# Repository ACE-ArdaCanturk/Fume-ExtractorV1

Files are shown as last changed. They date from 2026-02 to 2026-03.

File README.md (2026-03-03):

# Fume-ExtractorV1

This project wasn't originally meant to be shared and was more so something I built with parts I had on hand. This is why it includes weird parts like a neon bulb or a non standard inline fan, but I figured I might as well share it if anyone for some reason happened to have these parts on hand and wanted to build it, or to at least draw some inspiration for their own projects. It is a fume extractor for soldering consisting of one inline fan module with a 100mm radial fan and a bellmouth intake.

[Assembly Guide](AssemblyInstructions.md)

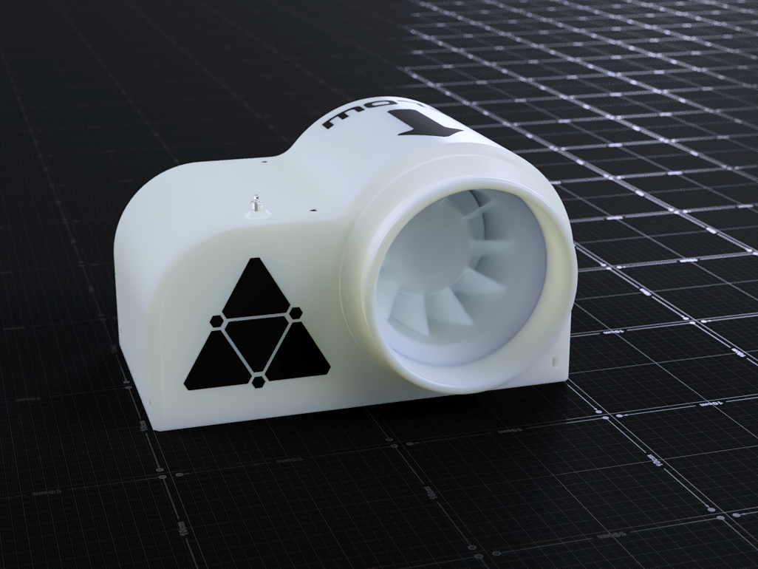
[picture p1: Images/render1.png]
Render1


# Media

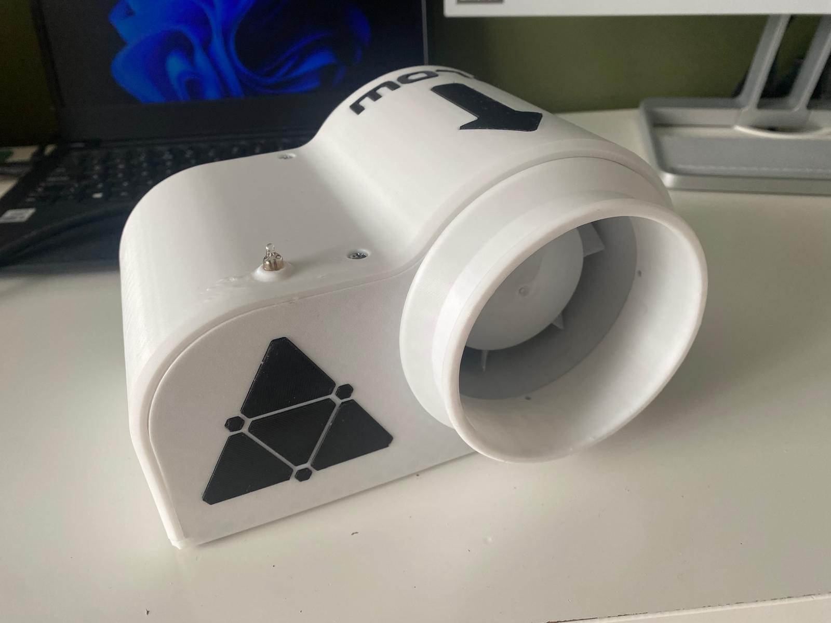
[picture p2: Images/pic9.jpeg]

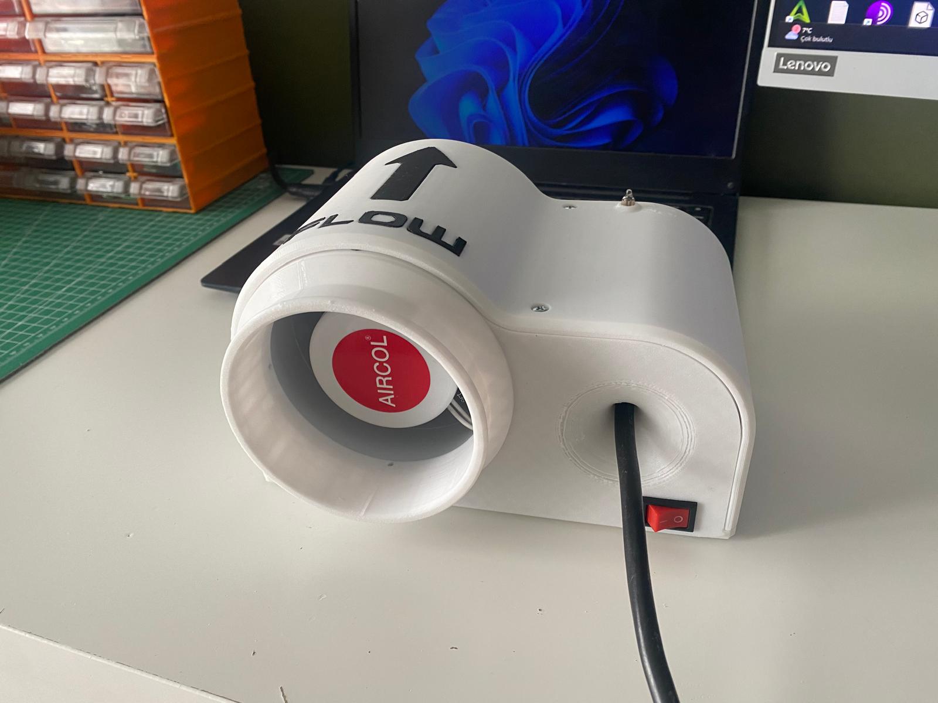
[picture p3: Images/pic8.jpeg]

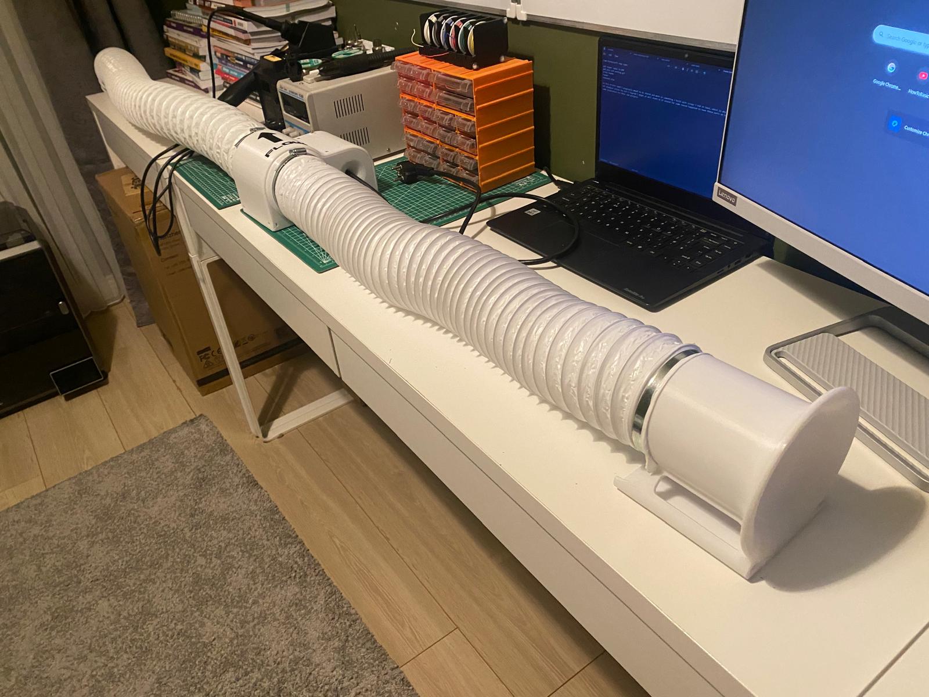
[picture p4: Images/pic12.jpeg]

gif2

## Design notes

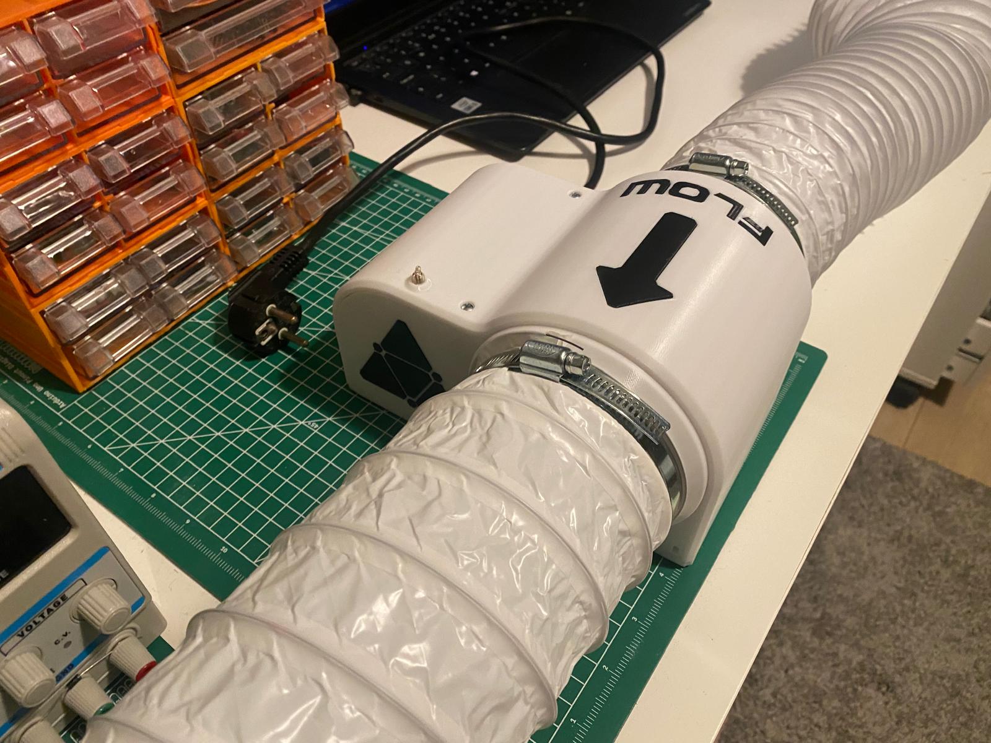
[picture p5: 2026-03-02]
Images/pic11.jpeg

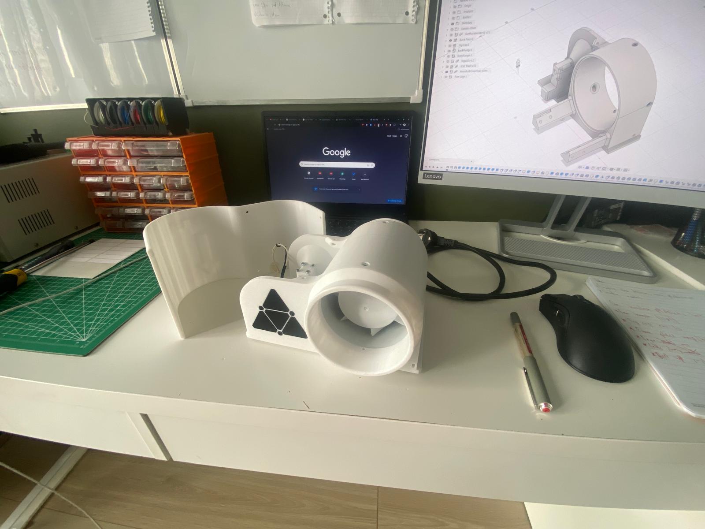
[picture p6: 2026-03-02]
Images/pic2.jpeg

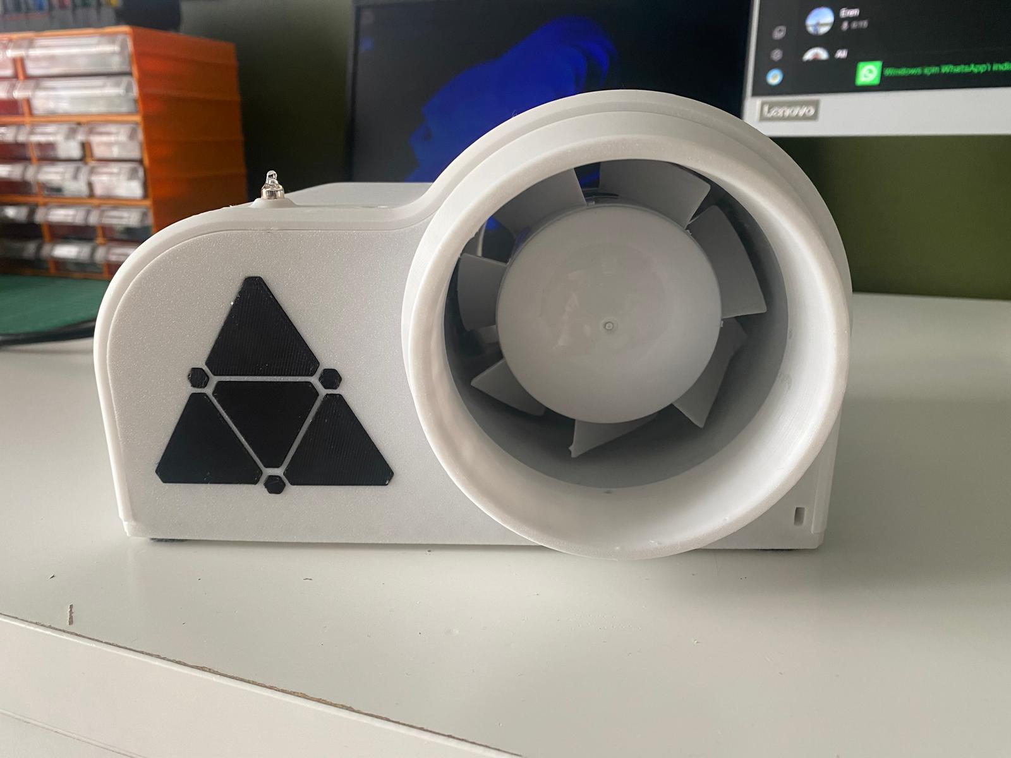
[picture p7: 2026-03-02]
Images/pic7.jpeg

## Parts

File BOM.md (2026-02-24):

## Bill of Materials (BOM): Fume-ExtractorV1

| Part Name | Description | Quantity | Link/Source |
| :--- | :--- | :--- | :--- |
| **Aircol 100KT** | 100mm AC Inline Fan | 1 | [Aksa Motor Fan](https://www.aksamotorfan.com/tr-TR/catalogue/kt-serisi/aircol-100-kt/1060/69) |
| **HVAC Tubing** | ID 100mm, Length 2000mm (200cm) | 2 | Local Hardware |
| **Hose Clamp** | 90-110mm Adjustable | 3 | Local Hardware |
| **Wago Connector** | 2-Pin Splicing Connector | 1 | Local Electronics |
| **AC Screw Terminal** | Wire-to-Wire Terminal Block | 1 | Local Electronics |
| **KCD1-101 Switch** | Rocker On/Off Switch | 1 | Local Electronics |
| **Neon Indicator** | 5mm Neon Lamp | 1 | Local Electronics |
| **AC Cable** | Standard Power Cord | 1 | Local Electronics |
| **M3x25mm Screw** | Roundhead Machine Screw | 2 | Local Hardware |
| **M3x20mm Screw** | Roundhead Machine Screw | 4 | Local Hardware |
| **M3x10mm Screw** | Roundhead Machine Screw | 11 | Local Hardware |
| **M3x5mm Screw** | Roundhead Machine Screw | 8 | Local Hardware |
| **M3 Nut** | Standard Hex Nut | 17 | Local Hardware |

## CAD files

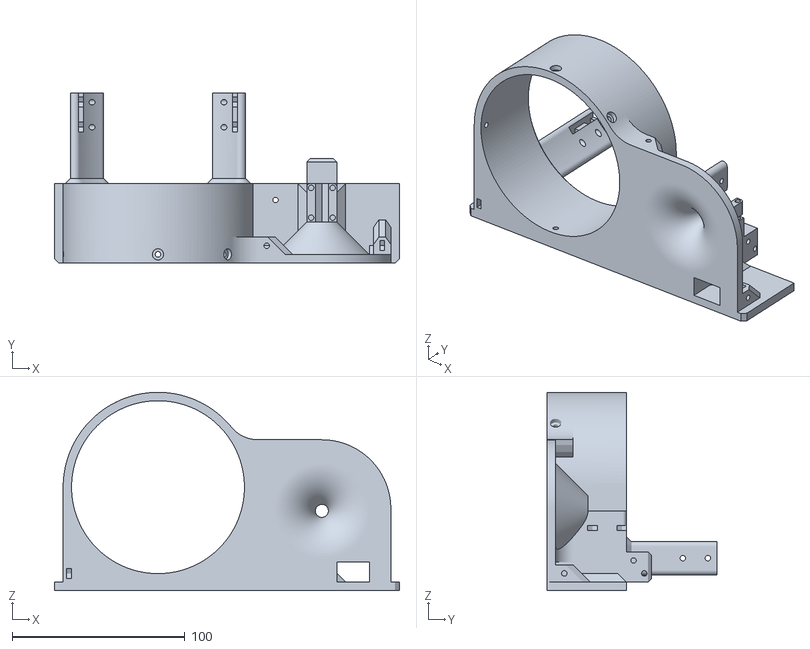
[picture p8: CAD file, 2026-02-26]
STLs/mainStructureBackPart.stl
200.0 x 98.5 x 115.0

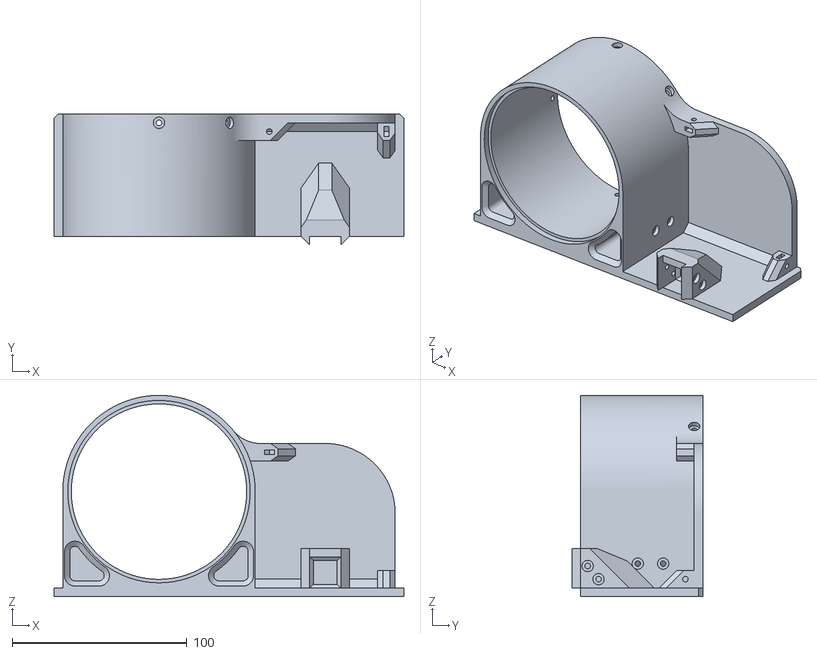
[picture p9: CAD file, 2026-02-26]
STLs/mainStructureFrontPart.stl
200.0 x 74.8 x 115.0

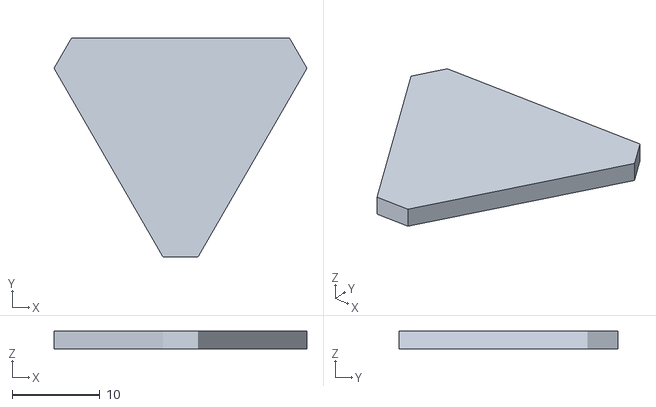
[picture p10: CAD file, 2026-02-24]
STLs/Lettering/logoMiddleTriangle.stl
28.9 x 25.0 x 2.00

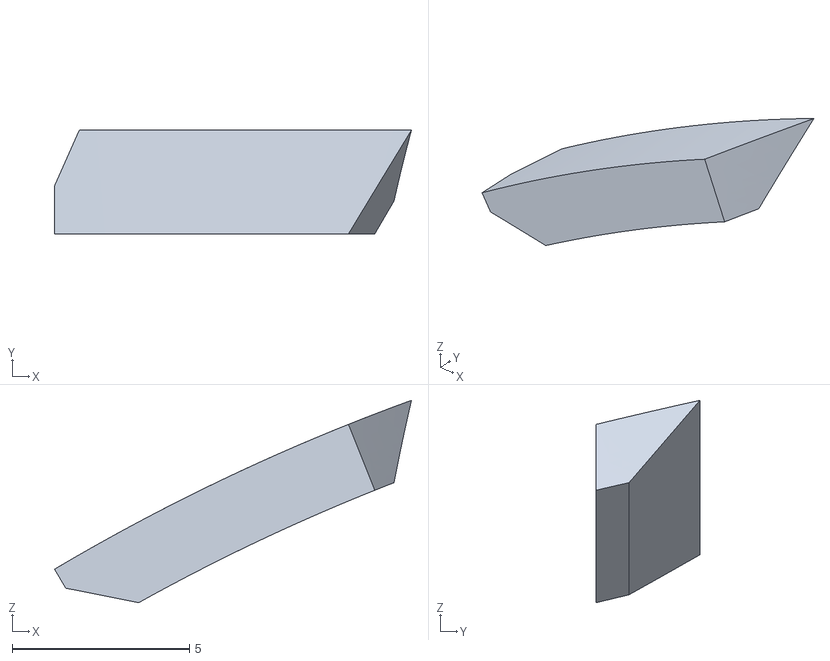
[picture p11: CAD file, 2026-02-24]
STLs/Lettering/letterFpart2.stl
10.1 x 2.93 x 5.71

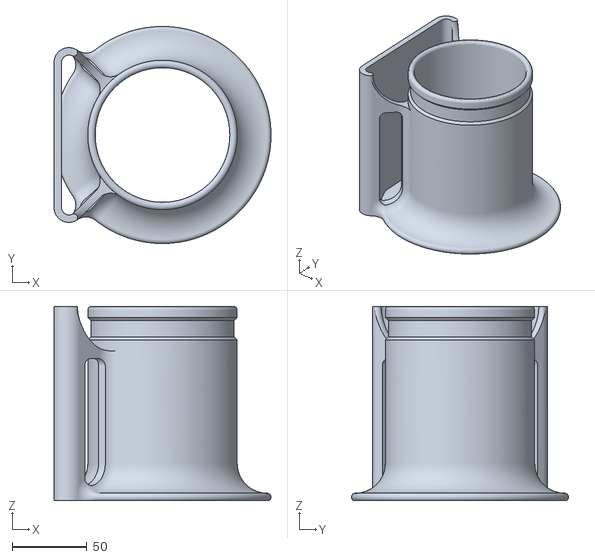
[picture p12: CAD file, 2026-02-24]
STLs/bellmouthIntake.stl
145.2 x 145.2 x 130.0

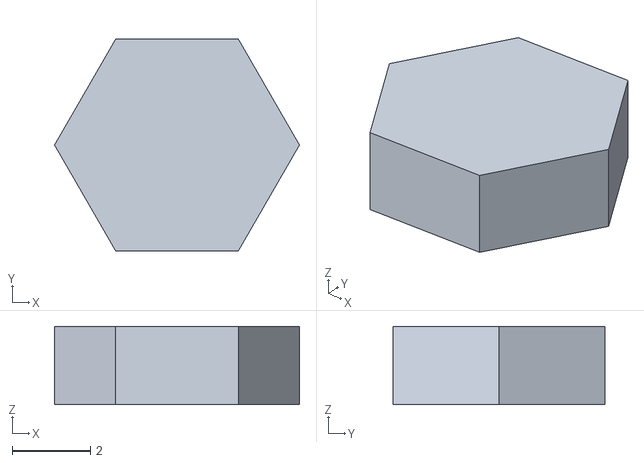
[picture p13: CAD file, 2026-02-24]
STLs/Lettering/logoHexagon3x.stl
6.27 x 5.43 x 2.00

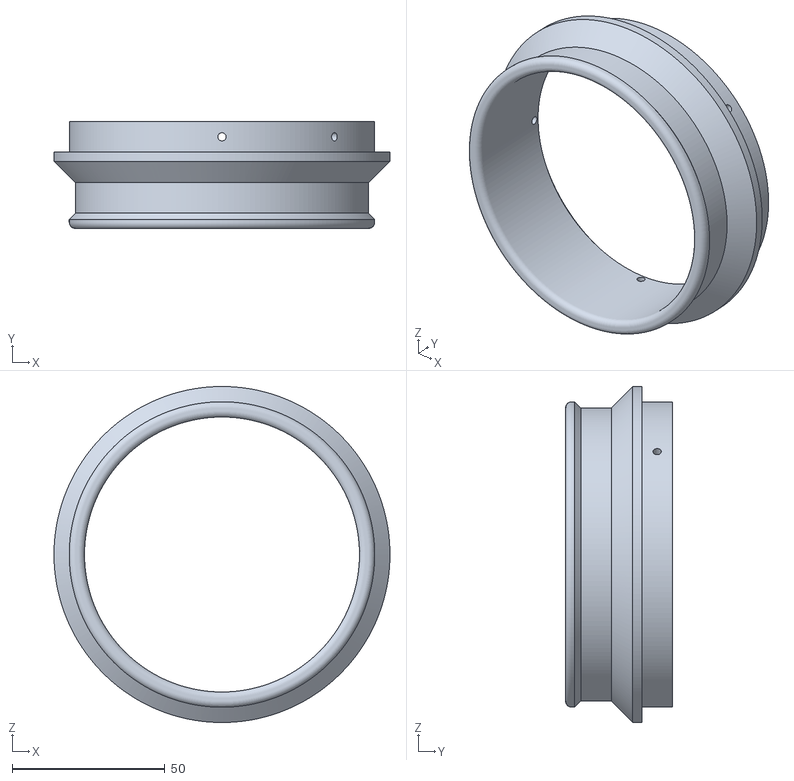
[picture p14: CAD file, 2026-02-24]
STLs/backFlange.stl
110.0 x 35.0 x 110.0

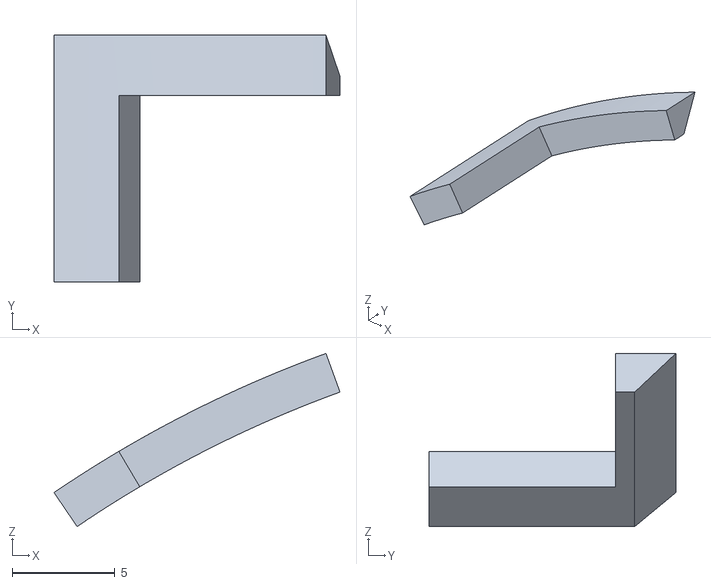
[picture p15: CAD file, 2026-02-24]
STLs/Lettering/letterFpart1.stl
13.9 x 12.0 x 8.43

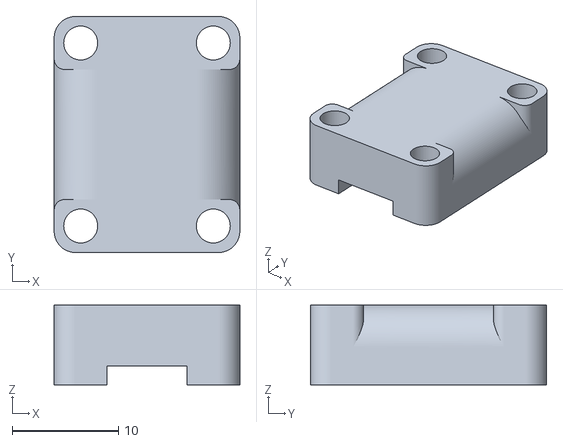
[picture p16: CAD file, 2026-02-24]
STLs/c_clamp.stl
17.5 x 22.2 x 7.50

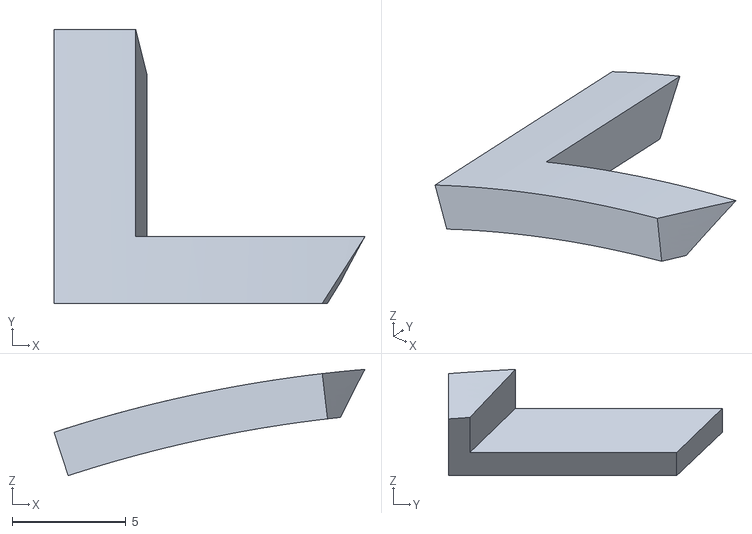
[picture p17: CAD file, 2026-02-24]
STLs/Lettering/letterL.stl
13.6 x 12.0 x 4.67

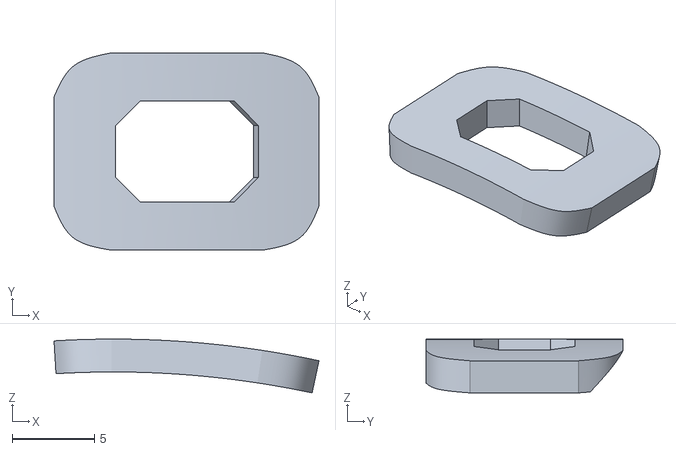
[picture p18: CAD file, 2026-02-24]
STLs/Lettering/letterO.stl
16.1 x 12.0 x 3.27

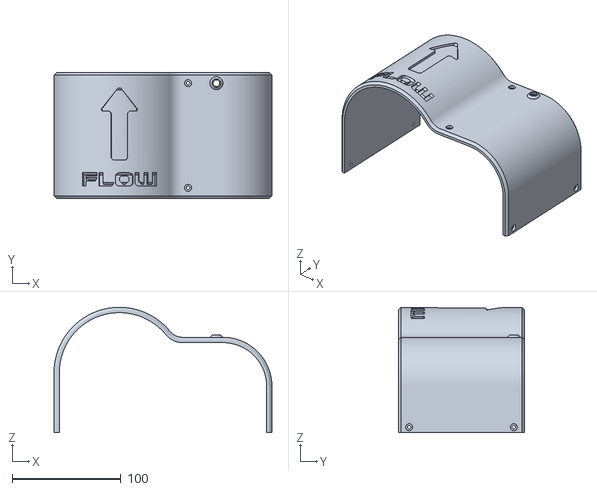
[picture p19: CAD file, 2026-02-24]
STLs/topCover.stl
200.0 x 116.0 x 115.0

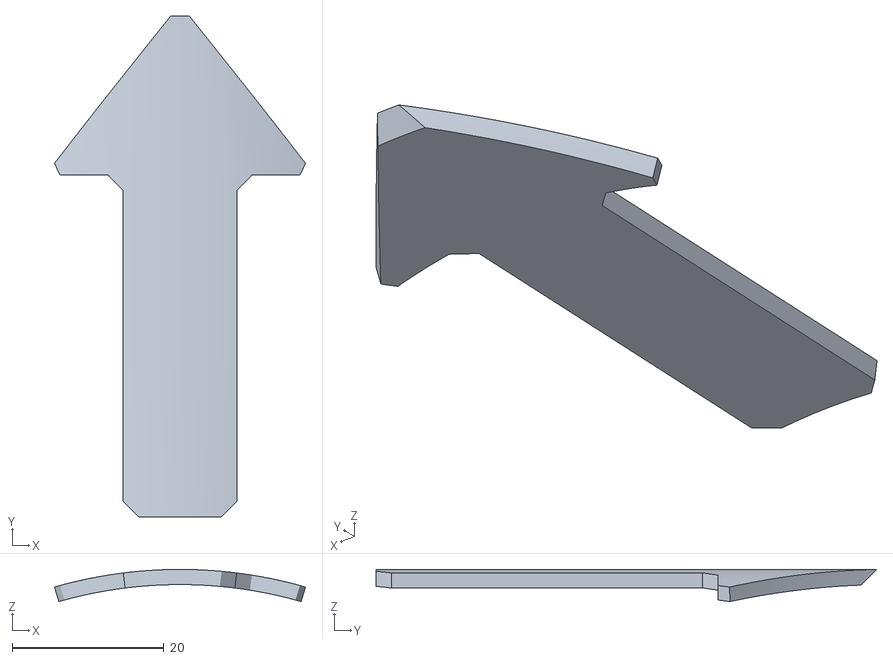
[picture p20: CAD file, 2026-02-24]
STLs/Lettering/letterUpArrow.stl
33.1 x 65.9 x 4.24

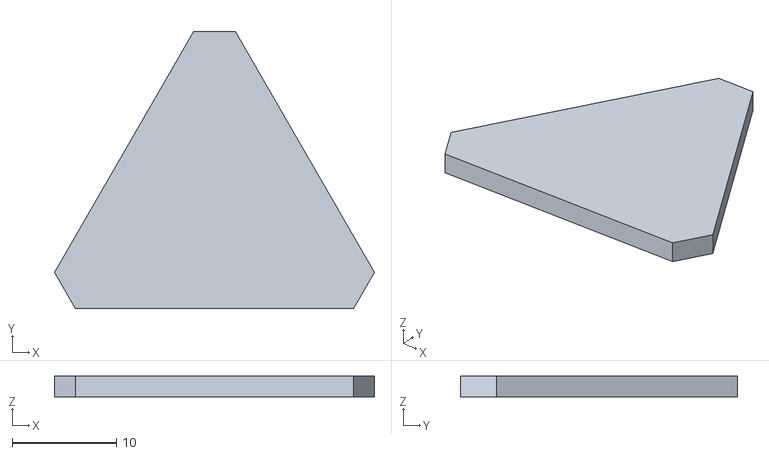
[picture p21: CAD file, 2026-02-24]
STLs/Lettering/logoSideTriangle3x.stl
30.6 x 26.5 x 2.00

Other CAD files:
STLs/frontFlange.stl
STLs/Lettering/letterW.stl
Fusion360 files/FumeExtractorFusionCAD.f3z
Fusion360 files/bellmouthIntake.f3d

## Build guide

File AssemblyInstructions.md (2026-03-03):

# Assembly Instructions 🛠️

## Required parts
Refer to the [BOM](BOM.md)

## Step 1: Printing

### General print parameters
(These were the settings i used you can adjust to your needs)

* Layer height: 0.2mm
* Infill: 15% Grid
* Nozzle size: 0.4mm
* Material: Petg

### Printing instructions
Everything in the STLs folder needs to be printed (except the lettering which is optional), special instructions are:

### Flanges
Both flanges should be printed with this orientation mating surface facing up, no supports, brim required.
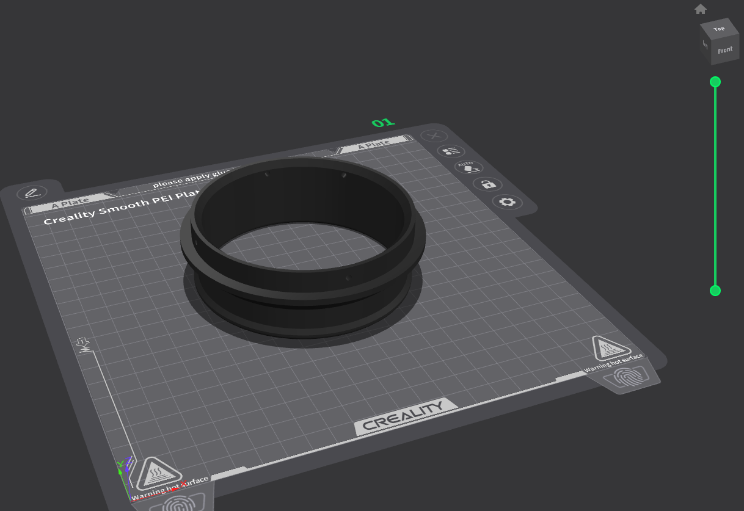
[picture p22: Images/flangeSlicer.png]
flangePic


### Main structure parts front/back
Should be printed flat side facing down. Front part will require supports where the emblem is, back part will require support where the cable inlet is located, brim is recommended for both parts to prevent warping.

### Top cover
Should be printed as such arrow looking up. No supports, brim required.
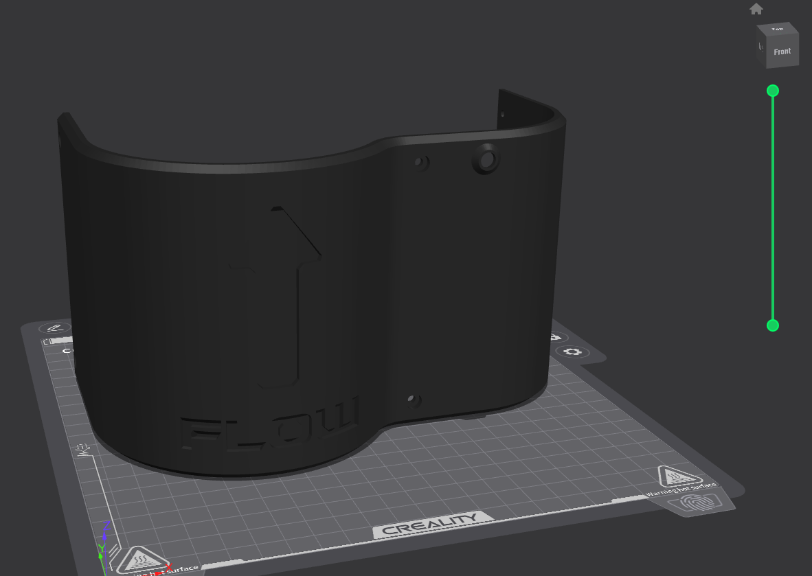
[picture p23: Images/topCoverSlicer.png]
topCoverPic


### C-Clamp
Printed on its back, no support or brim required.

### Bell mouth intake
Printed as such the curved inlet part facing the bed definitely needs support, no brim required.
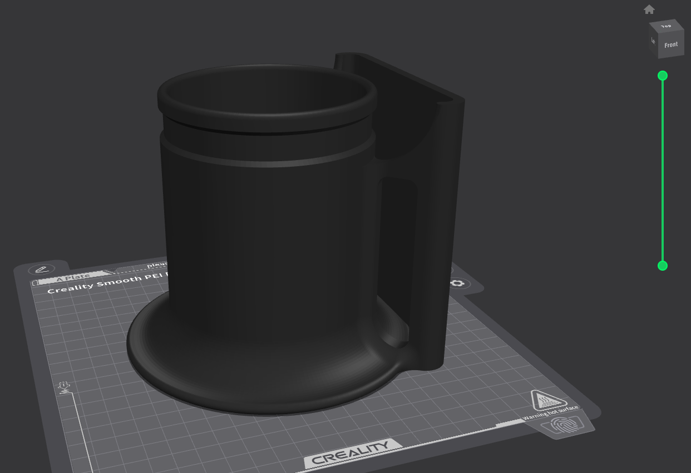
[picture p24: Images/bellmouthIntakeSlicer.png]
bellmouthPic


## Step 2: Assembly
***DISCLAIMER:*** This part of the guide will include fucking with ***high voltage*** AC electricity you can actually ***die*** if not careful, if you do then don't blame me. Proceed with ***caution***.

1) Start by fastening the flanges to their respective main structure parts using four m3x5mm screws for each, They will fasten directly into the flange plastic with no hex nuts.

2) Insert the fan inside the circular hole in the main structure back part, making sure to fish the fan cables into the cable hole as you do.

3) Insert four m3 hex nuts in the interlocking notches on back part.
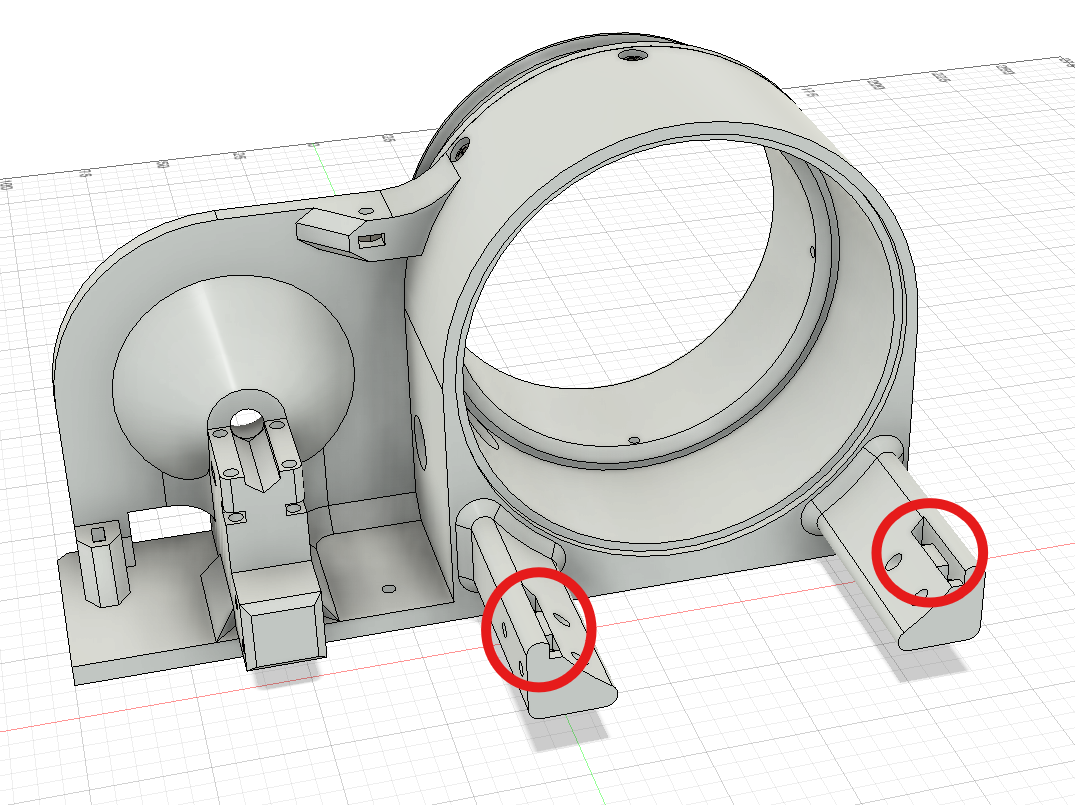
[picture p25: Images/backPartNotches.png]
backPartNotchesPic


4) Merge the front and back parts carefully and fasten four m3x10mm screws in places shown.
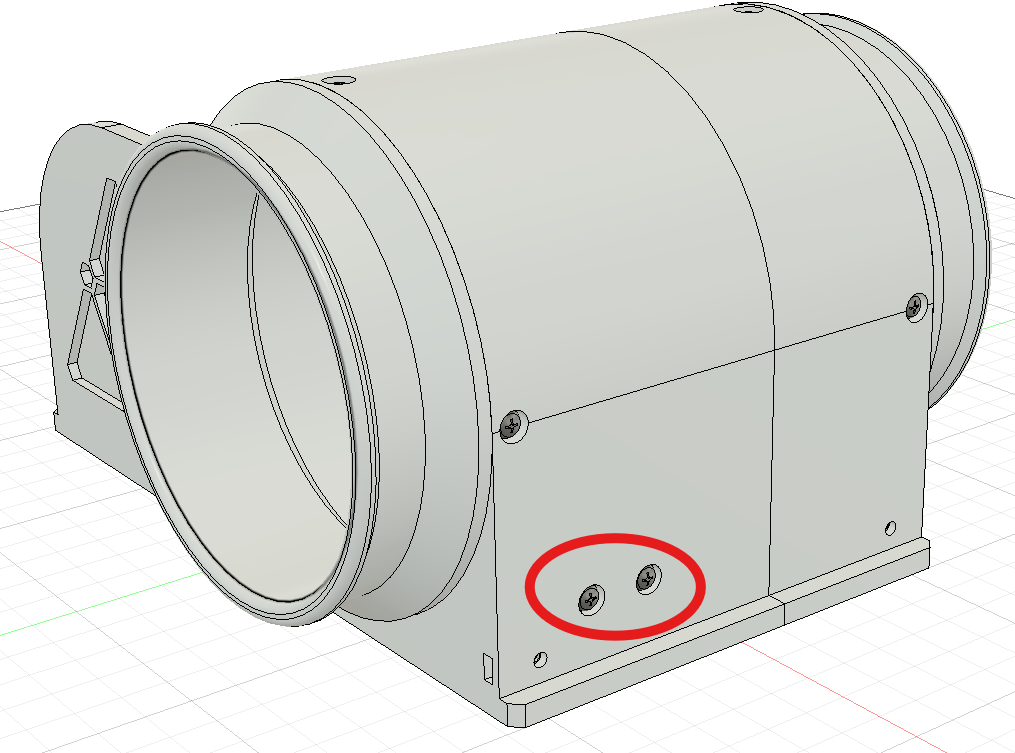
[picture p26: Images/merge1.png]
mergeFastenPic1

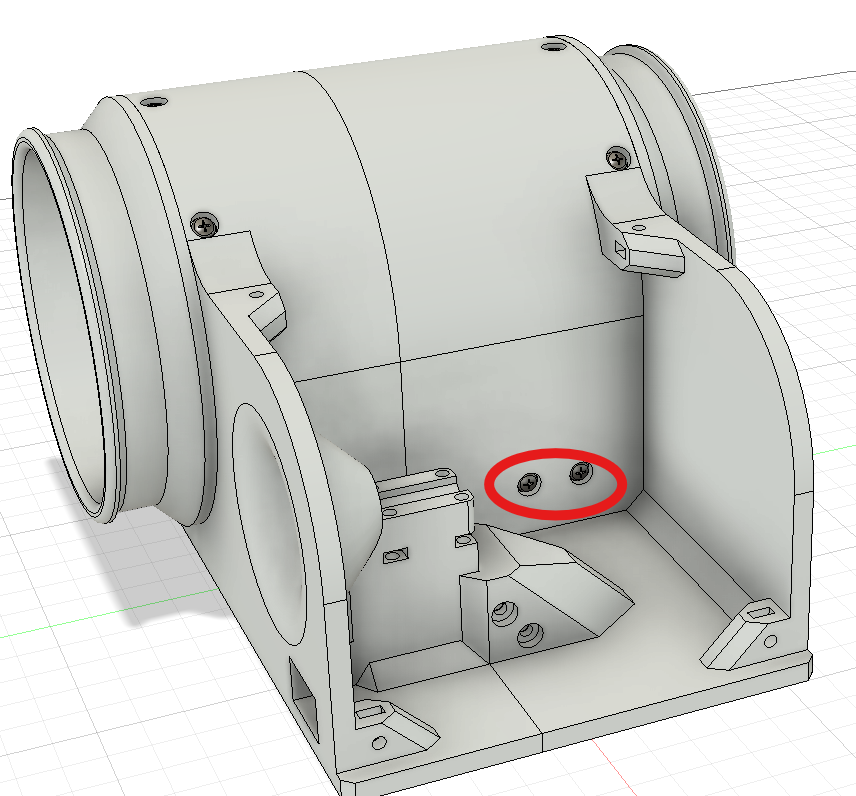
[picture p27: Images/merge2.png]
mergeFastenPic2


5) Fasten two m3x25mm screws with two hex nuts as shown.
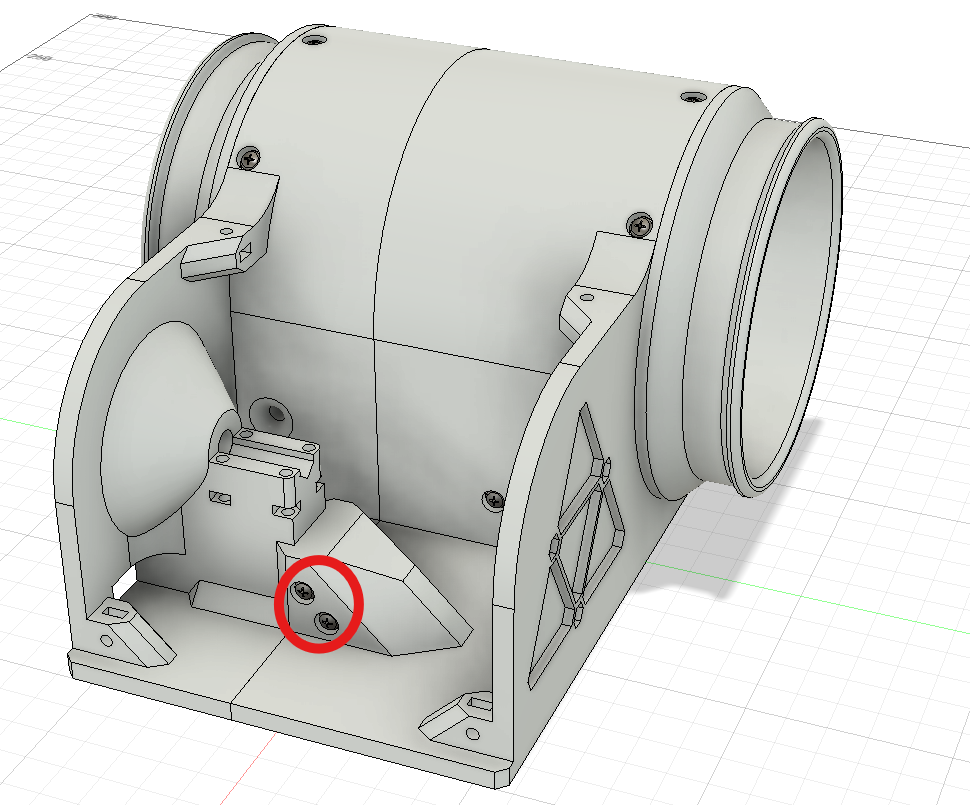
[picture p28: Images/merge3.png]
mergeFastenPic3

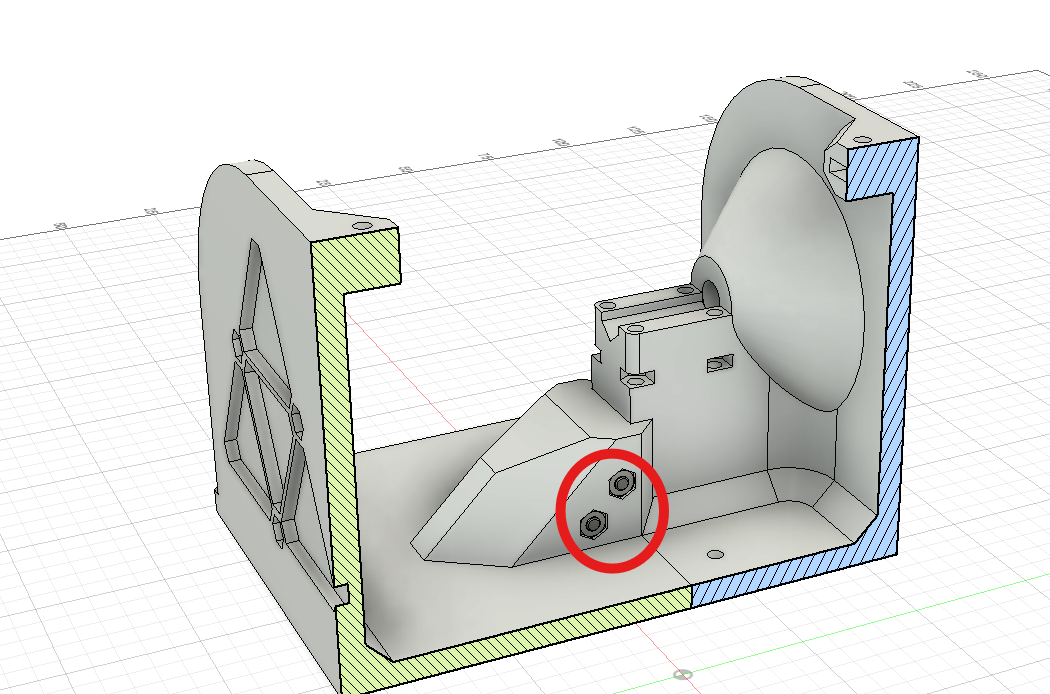
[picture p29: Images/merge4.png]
mergeFastenPic4


6) Insert the ac cable into the cable hole fasten it with the c-clamp using four m3x20mm screws and four hex nuts as shown. No need to overtighten the c-clamp tighten until you get good compression and give it a firm pull to see if its secure, do not tighten all the way.
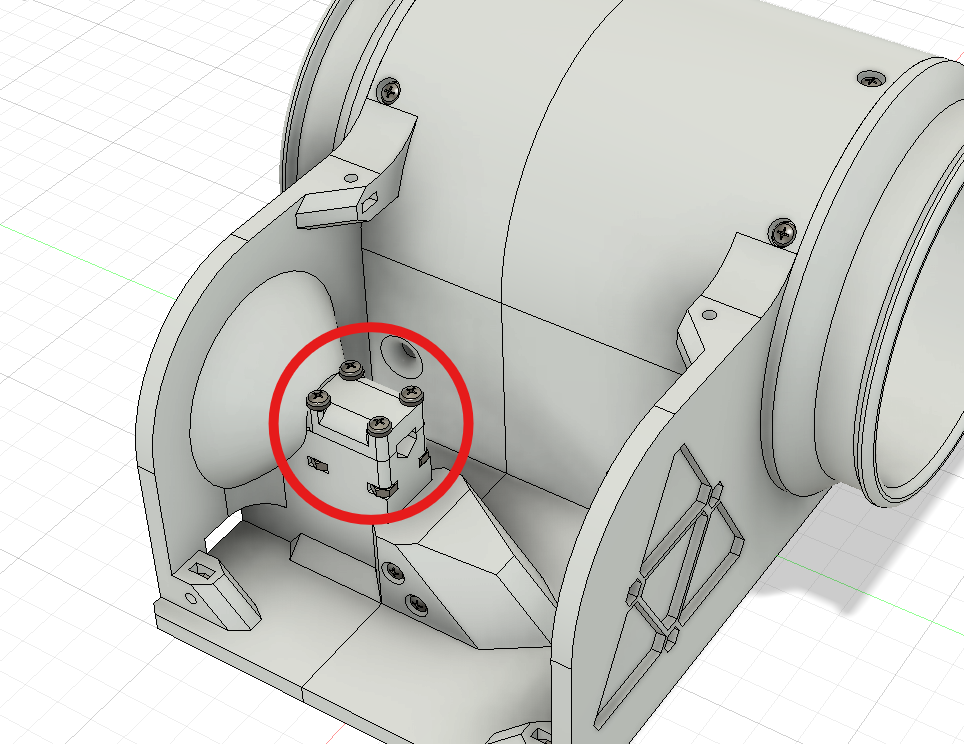
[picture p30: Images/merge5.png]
mergeFastenPic5


7) Take your on/off switch solder two 15cm length copper wires to the spade terminals, and insert it into its place (make sure to heatshrink the solder joints).
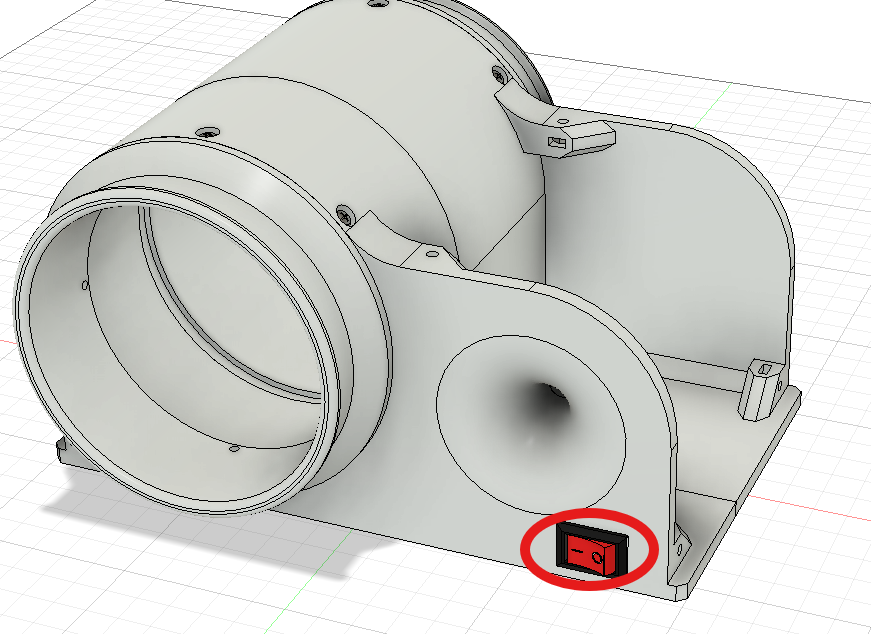
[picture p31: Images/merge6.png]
mergeFastenPic6


8) Insert your neon bulb in its place on the top cover glue it in place using super glue or hot glue (solder extension wires to the bulbs leads if theyre not long enough to connect to the screw terminal)
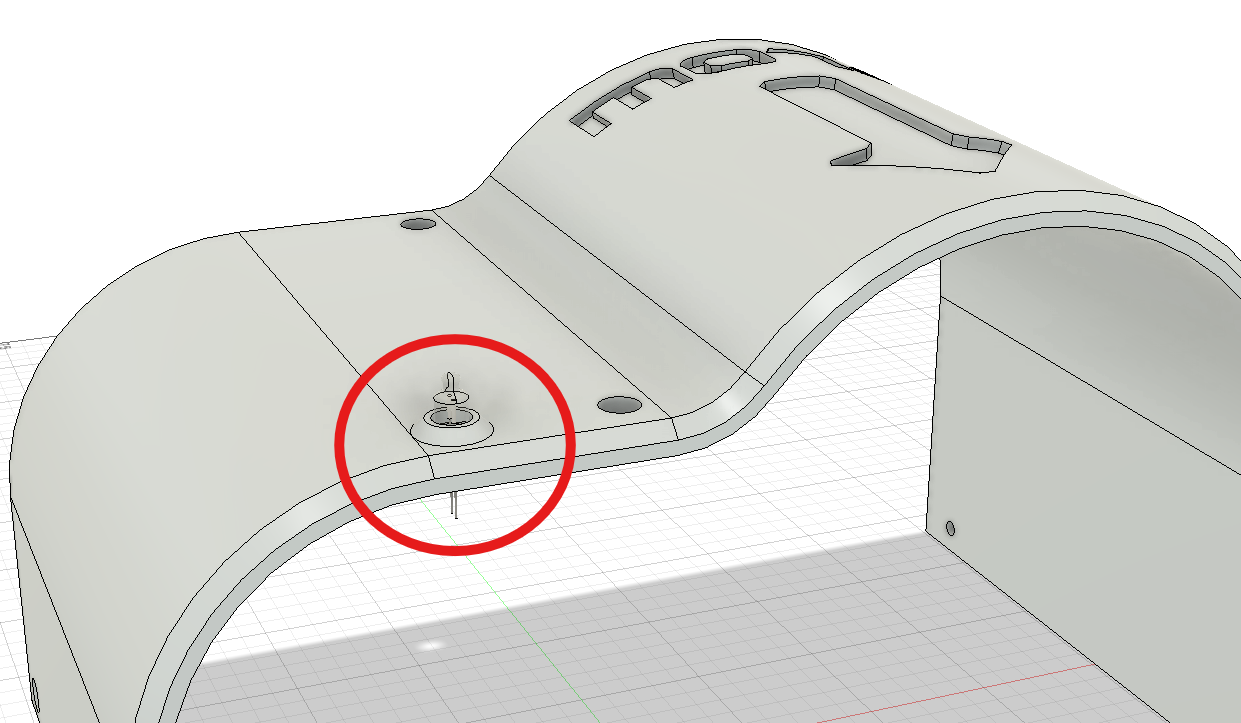
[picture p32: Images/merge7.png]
mergeFastenPic7


9) Do the cabling according to this schematic.
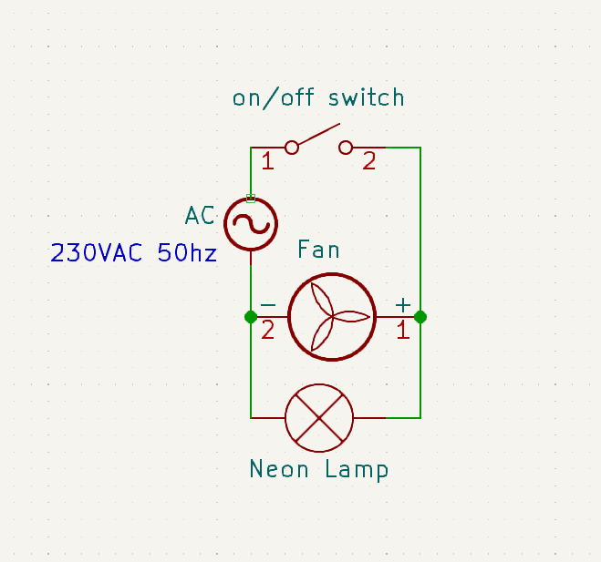
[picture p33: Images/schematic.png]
schematic


How to do it is up to you but i did it as such, live ac wire interrupted by the switch connected together with a wago connector and the output of the switch is connected to one side of the screw terminal, neutral ac wire is directly connected to the other side of the screw terminal. Also the neon bulb is wired in parallel into the screw terminal block in the exact places where the ac cables were inserted. Then on the opposite side of the terminal block the fan wires are connected also in parallel to the circuit, the terminal block is screwed down with a m3x10mm screw plus a hex nut and thats it. Irl photos for reference.
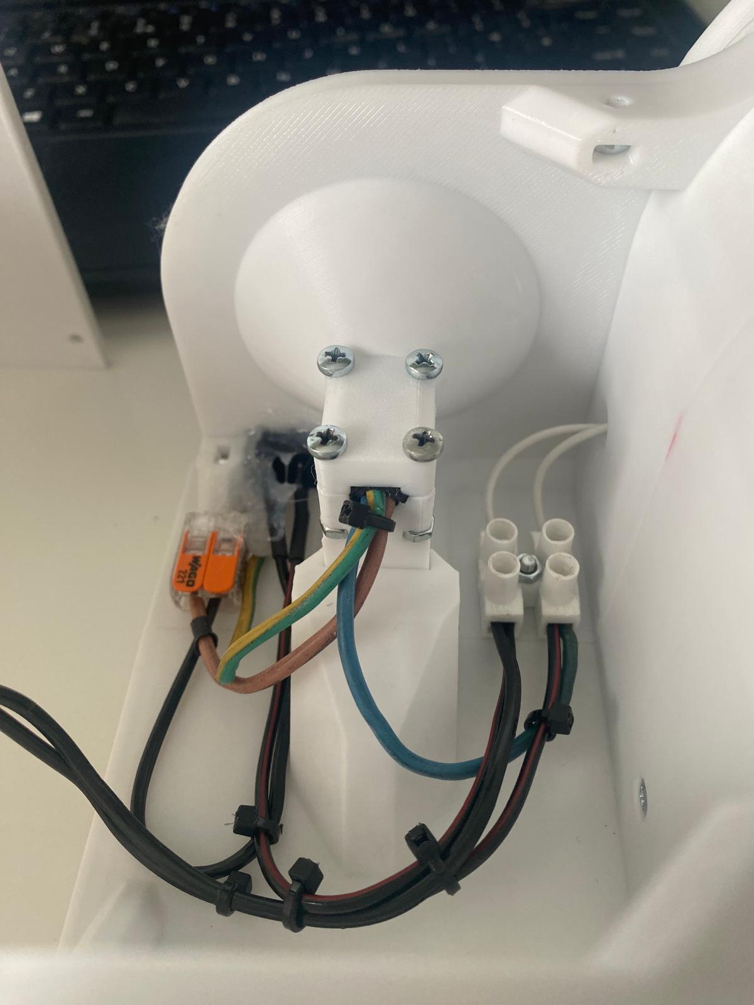
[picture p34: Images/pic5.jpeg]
wiring1

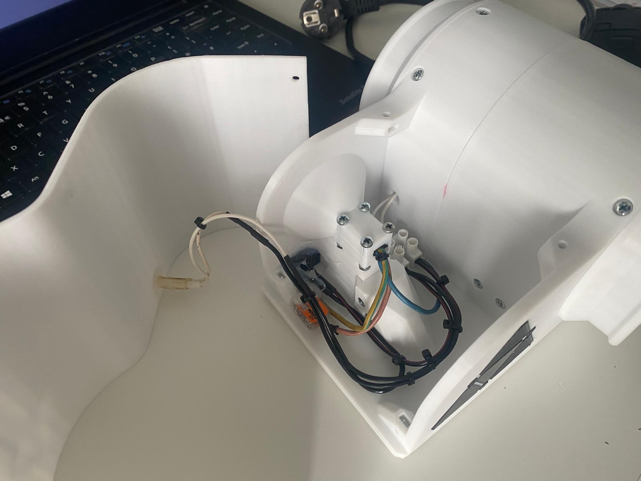
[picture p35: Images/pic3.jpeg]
wiring2

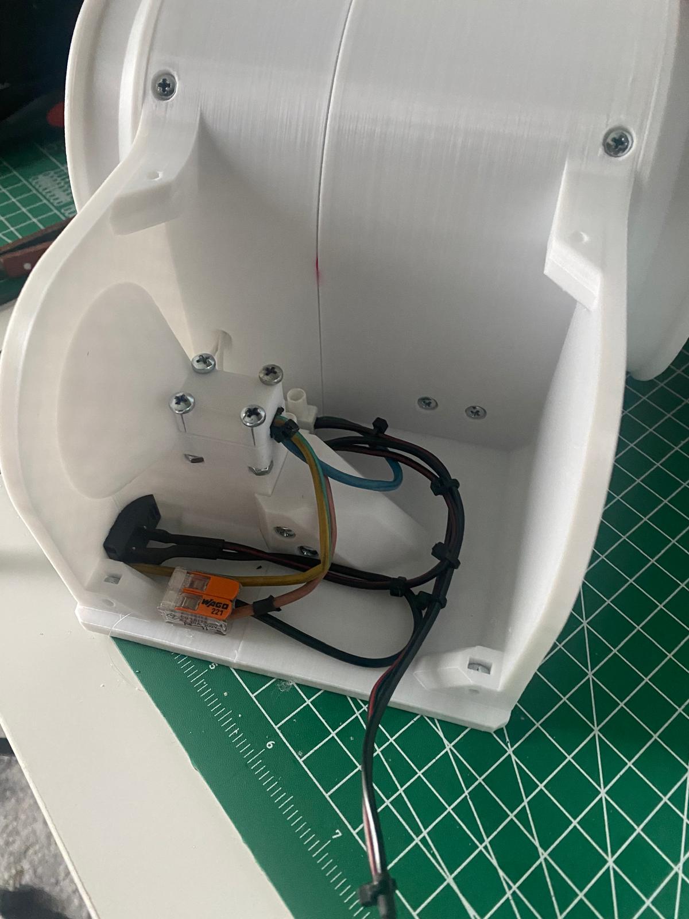
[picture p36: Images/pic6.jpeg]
wiring3

Additionally i glued the wago down with a drop of hot glue, tidied everything up with zipties and tucked the ground wire to the side with hotglue since we don't need it and i dont want it wiggling around in there.

10) Insert six hex nuts in total as shown.
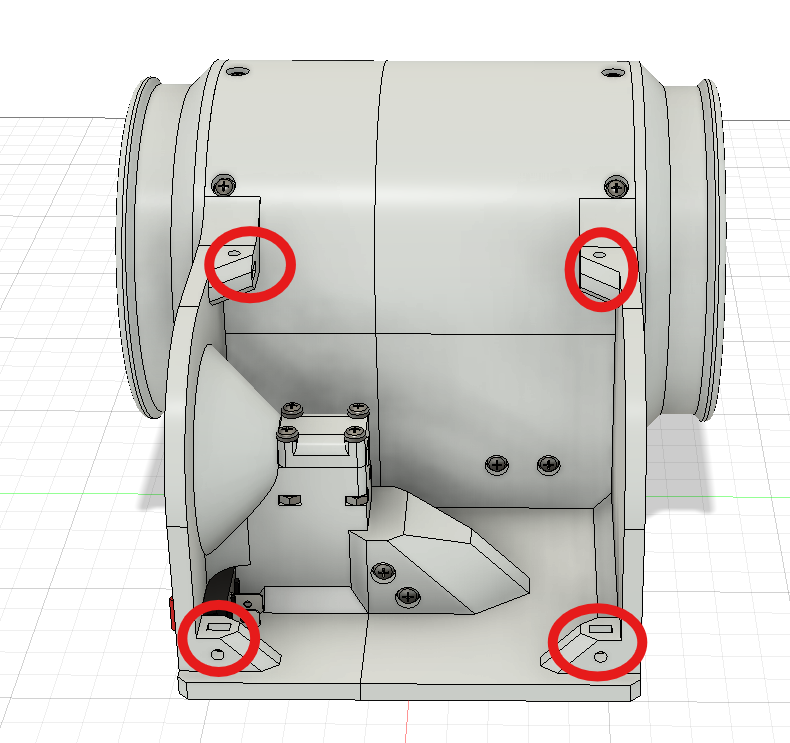
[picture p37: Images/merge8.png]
mergeFastenPic8

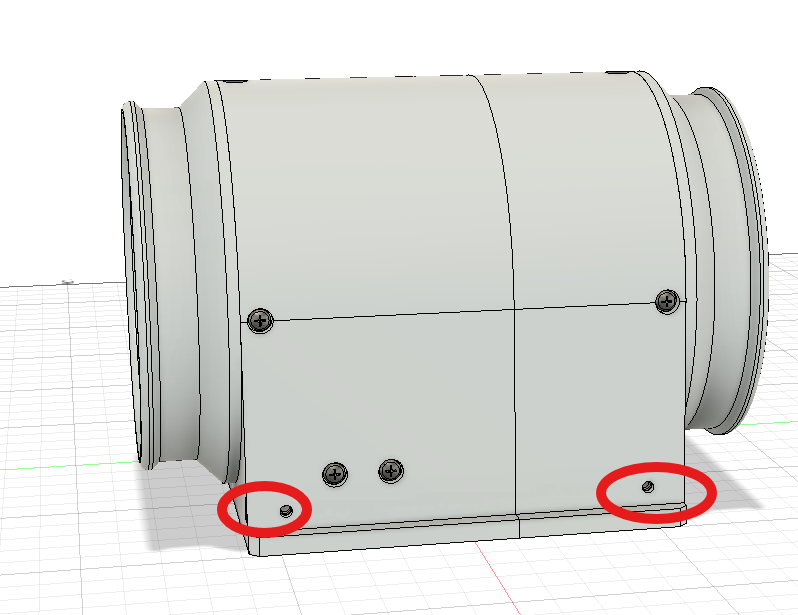
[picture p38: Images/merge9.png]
mergeFastenPic9


11) Screw down the top cover using six m3x10mm screws.
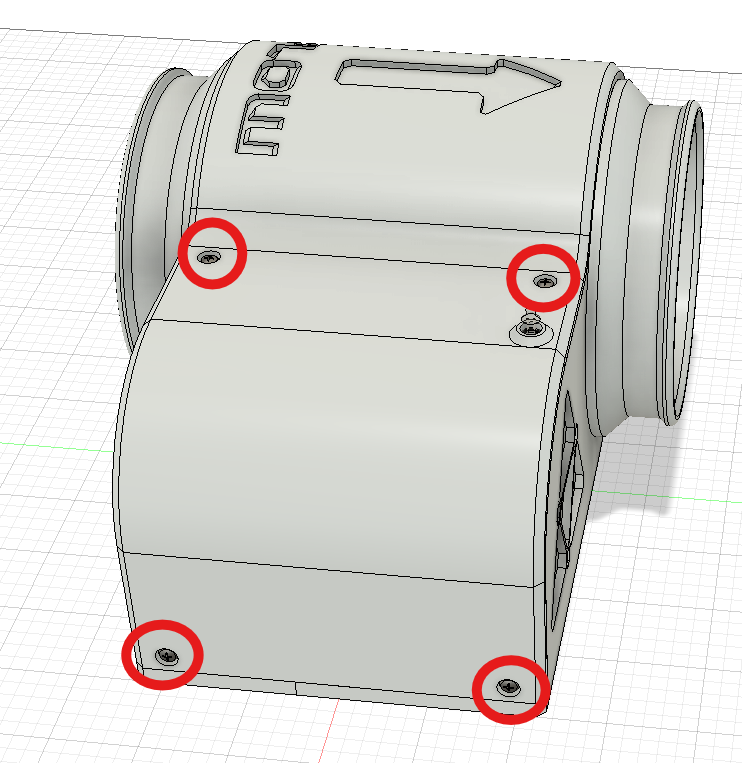
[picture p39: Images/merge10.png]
mergeFastenPic10

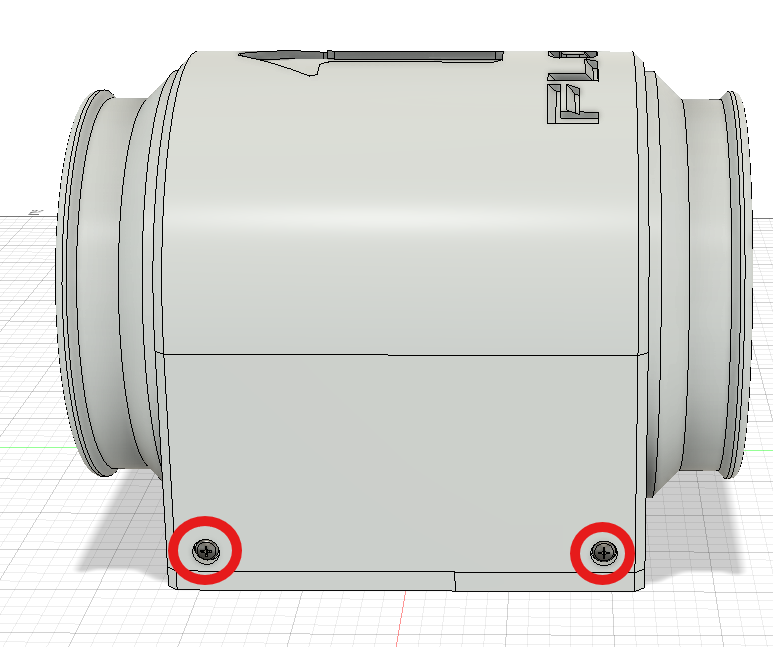
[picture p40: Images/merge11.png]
mergeFastenPic11


## Done ✅
That is it from the assembly. Additionally you can print the lettering and glue them in place but otherwise you should have a functional fume extractor, connect it together with the intake using hvac hosing and test it.

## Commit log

2026-02-24 added stls
    [backFlange.stl, c_clamp.stl, frontFlange.stl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]
2026-02-24 added fusion360 assembly file
    [FumeExtractorFusionCAD.f3z]
2026-02-24 file name changes
    [FumeExtractorFusionCAD.f3z]
2026-02-24 added bellmouth intake
    [bellmouthIntake.f3d, bellmouthIntake.stl]
2026-02-24 added bill of materials
2026-02-24 added schematic/updated f3z file
    [FumeExtractorFusionCAD.f3z]
2026-02-26 updated stls
    [FumeExtractorFusionCAD.f3z]
2026-03-03 updated installation.md
    [mainStructureBackPart.stl, mainStructureFrontPart.stl, topCover.stl]
2026-03-03 finalized assembly instructions
